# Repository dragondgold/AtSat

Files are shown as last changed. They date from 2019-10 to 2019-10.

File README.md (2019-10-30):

<h2>
</a>Desarrollo de satélite CanSat para
utilizar como plataforma educativa y
fomentar el interés en ingenierías</h2>

El objetivo principal del proyecto es el de proveer un satélite tipo CanSat completamente funcional y listo para ser utilizado, 
con una Estación Terrena para la comunicación con el mismo, a modo de plataforma educativa que permite no solo ser utilizada 
por estudiantes sin modificación alguna, sino que provee la capacidad de ser expandida para agregar o mejorar las funcionalidades 
básicas dando lugar a los estudiantes a experimentar libremente sobre una plataforma segura.

A su vez, la plataforma sera diseñada siguiendo la normativa impuesta por la European Space Agency (ESA) 
lo cual dará la posibilidad a futuro de participar de competencias de CanSat.

El proyecto está pensado para que el CanSat pueda alcanzar una altura máxima de
1000 metros aproximadamente y realice un descenso con la ayuda de un paracaídas que
limitará su velocidad para evitar la destrucción del mismo al impactar contra el suelo.
Durante esta etapa también se realizará la medición de las variables
que envía el CanSat a la Estación Terrena para luego ser interpretadas. Esto permite
analizar diversos factores respecto a la altura como los niveles de contaminación del
aire, la variabilidad de la temperatura y presión atmosférica, la toma de imágenes para
su posterior procesamiento, medición de radiación UV, composición gaseosa del aire,
etcétera.

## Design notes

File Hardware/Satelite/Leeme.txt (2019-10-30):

PCB_A -> RF + Conectores servos + Anclaje al satelite + Conexión batería + GPS + Switch y LEDs
PCB_B -> Reguladores + Protecciones + Gestión Batería
PCB_C -> Sensores + MCU Supervisor + Conector expansión limitado + micro-usb
PCB_D -> Arduino + micro-usb + Conector expansion
PCB_E -> Plaqueta preperforada + Conector expansion

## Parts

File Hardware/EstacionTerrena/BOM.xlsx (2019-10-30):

Component | Description | Part | References | Value | Footprint | Quantity Per PCB | Manufacturer Part Number
1 | Unpolarized capacitor, small symbol | C_Small | C6 C7 C8 C11 C12 C13 C14 | 100nF | C_0402_1005Metric | 7 | GCM155R71C104KA55D | 1
2 | Unpolarized capacitor, small symbol | C_Small | C2 C4 | 100nF | C_0603_1608Metric | 2 | EMK107B7104KAHT
3 | Unpolarized capacitor, small symbol | C_Small | C17 | 100pF | C_0402_1005Metric | 1 | 885012005046 | 1
4 | Unpolarized capacitor, small symbol | C_Small | C9 C10 | 15pF | C_0402_1005Metric | 2 | C0402C150J5GACTU | 1
5 | Unpolarized capacitor, small symbol | C_Small | C5 | 1uF | C_0603_1608Metric | 1 | LMK107B7105MA-T
6 | Unpolarized capacitor, small symbol | C_Small | C1 C3 | 2.2uF | C_0805_2012Metric | 2 | LMK212B7225KG-T | 1
7 | Light emitting diode | LED | D2 | Rojo | LED_0603_1608Metric | 1 | 150060RS75000 | 1
8 | Light emitting diode | LED | D1 | Verde | LED_0603_1608Metric | 1 | 150060VS75000 | 1
9 | SUBMINIATURE COAX | 5-1814832-1 | + | 5-1814832-1 | 5-1814832-1 | 1 | 5-1814832-1 | 1
10 | Generic connector, single row, 01x03, script generated (kicad-library-utils/schlib/autogen/connector/) | Conn_01x03 | J3 | Conn_01x03 | PinHeader_1x03_P2.54mm_Horizontal | 1 | 61300311121
11 | USB Micro Type B connector | USB_B_Micro | J2 | USB_B_Micro | USB_Micro-B_Molex-105017-0001 | 1 | 105017-0001
12 |  | BOM_Jumper | JP1 | BOM_Jumper | Empty_Footprint | 1 | M7581-05
13 | Inductor | L | L1 | 12nH | L_0402_1005Metric | 1 | L-07C12NJV6 | 1
14 | Resistor | R | R5 R6 | 0R | R_0402_1005Metric | 2 | RC0402JR-070RL | 1
15 | Resistor | R | R3 | 10k | R_0603_1608Metric_Pad1.05x0.95mm_HandSolder | 1 | RC0603JR-0710KL
16 | Resistor | R | R1 R2 | 220 | R_0603_1608Metric_Pad1.05x0.95mm_HandSolder | 2 | RC0603JR-13220RL
17 | Resistor | R | R4 | 56k | R_0402_1005Metric | 1 | RC0402FR-0756KL | 1
18 | Signal Conditioning 915MHz BALUN/FILTER | 0915BM15A0001E | U5 | 0915BM15A0001E | 0915BM15A0001E | 1 | 0915BM15A0001E | 1
19 | Texas Instruments CC1101RGP, RF Transceiver IC Triple Band 1.8 3.6 V 20-Pin QFN | CC1101RGP | U4 | CC1101RGP | QFN50P400X400X100-21N-D | 1 | CC1101RGP | 1
20 | USB-to-SPI Protocol Converter with GPIO (Master Mode) | MCP2210 | U3 | MCP2210 | SSOP-20_5.3x7.2mm_P0.65mm | 1 | MCP2210-I/SS | 1
21 | Micrel MIC5323-3.3YD5 TR, LDO Voltage Regulator, 300mA, 3.3 V 2%, 2.65 5.5 Vin, 5-Pin TSOT-23 | MIC5323-3.3YD5_TR | U2 | MIC5323-3.3YD5_TR | SOT95P280X100-5N | 1 | MIC5323-3.3YD5 TR | 1
22 | Dual-Channel High-Speed ESD Protection | TPD2E2U06 | U1 | TPD2E2U06 | SOT-553 | 1 | TPD2E2U06DRLR | 1
23 | Three pin crystal, GND on pin 2 | Crystal_GND2 | Y1 | 12MHz | Resonator_SMD_muRata_CSTxExxV-3Pin_3.0x1.1mm | 1 | CSTNE12M0GH5L000R0 | 1
24 | Four pin crystal, GND on pins 2 and 4 | Crystal_GND24 | Y2 | 26 MHz | Crystal_SMD_2520-4Pin_2.5x2.0mm | 1 | FA-20H 26.0000MF12V-W | 1

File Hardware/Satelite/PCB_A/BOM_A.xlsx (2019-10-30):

Component | Description | Part | References | Value | Footprint | Quantity Per PCB | Manufacturer Part Number
1 | Unpolarized capacitor, small symbol | C_Small | C2 C4 C5 C6 C9 C10 C11 C12 | 100nF | C_0402_1005Metric | 8 | GCM155R71C104KA55D
2 | Unpolarized capacitor, small symbol | C_Small | C15 | 100pF | C_0402_1005Metric | 1 | 885012005046
3 | Unpolarized capacitor, small symbol | C_Small | C7 C8 | 15pF | C_0402_1005Metric | 2 | C0402C150J5GACTU
4 | Unpolarized capacitor, small symbol | C_Small | C1 C3 | 1uF | C_0603_1608Metric_Pad1.05x0.95mm_HandSolder | 2 | LMK107B7105MA-T
5 | Light emitting diode | LED | D1 | Rojo | LED_0603_1608Metric_Pad1.05x0.95mm_HandSolder | 1 | 150060RS75000
6 | Light emitting diode | LED | D2 | Verde | LED_0603_1608Metric_Pad1.05x0.95mm_HandSolder | 1 | 150060VS75000
7 | Resettable fuse, polymeric positive temperature coefficient | Polyfuse | F1 | Polyfuse | Fuse_1812_4532Metric_Pad1.30x3.40mm_HandSolder | 1 | 0ZCG0150FF2C
8 | RF Connectors / Coaxial Connectors U.FL Straight Surface Mount Jack | CONUFL001-SMD | J2 | CONUFL001-SMD | CONUFL001-SMD | 1 | CONUFL001-SMD
9 |  | Conector_PCB_A-B | J4 | Conector_PCB_A-B | Conector_PCB_A-B | 3 | 22-28-5034
10 |  |  | J4 | Conector_PCB_A-B | Conector_PCB_A-B | 2 | 22-28-4041
11 | Generic connector, single row, 01x03, script generated (kicad-library-utils/schlib/autogen/connector/) | Conn_01x03 | J3 | Servo Globo | PinHeader_1x03_P2.54mm_Vertical | 1 | 61300311121
12 | Generic connector, single row, 01x03, script generated (kicad-library-utils/schlib/autogen/connector/) | Conn_01x03 | J5 | Servo ParacaÃdas | PinHeader_1x03_P2.54mm_Vertical | 1 | 61300311121
13 | Inductor | L | L1 | 12nH | L_0402_1005Metric | 1 | L-07C12NJV6
14 |  | Spacer | M1 M2 M3 | Spacer | Empty_Footprint | 3 | R30-3011002
15 | 0.8A Ic, 45V Vce, NPN Transistor, SOT-23 | BC817 | Q2 | BC817 | SOT-23 | 1 | BC817-16LT1G
16 | MOSFET Small-signal MOSFET Vdss= -12V, ID= -6A | SSM3J338R,LF | Q1 | SSM3J338R,LF | SSM3J332RLFT | 1 | SSM3J338R,LF
17 | Resistor | R | R9 R10 | 0R | R_0402_1005Metric | 2 | RC0402JR-070RL
18 | Resistor | R | R3 R4 R5 R6 R7 | 10k | R_0603_1608Metric_Pad1.05x0.95mm_HandSolder | 5 | RC0603JR-0710KL
19 | Resistor | R | R1 R2 | 1k | R_0603_1608Metric_Pad1.05x0.95mm_HandSolder | 2 | RC0603JR-071KL
20 | Resistor | R | R8 | 56k | R_0402_1005Metric | 1 | RC0402FR-0756KL
21 | Slide Switches SPDT RA SLIDE PC MNT | 500SSP1S1M6QEA | S1 | 500SSP1S1M6QEA | 500SSP1S1M6QEA | 1 | 500SSP1S1M6QEA
22 | Signal Conditioning 915MHz BALUN/FILTER | 0915BM15A0001E | U3 | 0915BM15A0001E | 0915BM15A0001E | 1 | 0915BM15A0001E
23 | GPS Modules SiRFStarIV GPS receiver SMT ROM mod | A2235-H | U1 | A2235-H | A2235-H | 1 | A2235-H
24 | Texas Instruments CC1101RGP, RF Transceiver IC Triple Band 1.8 3.6 V 20-Pin QFN | CC1101RGP | U2 | CC1101RGP | QFN50P400X400X100-21N-D | 1 | CC1101RGP
25 | Four pin crystal, GND on pins 2 and 4 | Crystal_GND24 | Y1 | 26 MHz | Crystal_SMD_2520-4Pin_2.5x2.0mm | 1 | FA-20H 26.0000MF12V-W

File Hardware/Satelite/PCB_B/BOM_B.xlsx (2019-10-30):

Component | Description | Part | References | Value | Footprint | Quantity Per PCB | Manufacturer Part Number
1 | Unpolarized capacitor, small symbol | C_Small | C27 | 0.47uF | C_0603_1608Metric_Pad1.05x0.95mm_HandSolder | 1 | 885012206024
2 | Unpolarized capacitor, small symbol | C_Small | C4 C7 C11 C13 C15 C21 C22 | 100nF | C_0603_1608Metric_Pad1.05x0.95mm_HandSolder | 7 | EMK107B7104KAHT
3 | Unpolarized capacitor, small symbol | C_Small | C19 | 10n | C_0603_1608Metric_Pad1.05x0.95mm_HandSolder | 1 | 06033C103K4T2A
4 | Unpolarized capacitor, small symbol | C_Small | C1 C2 C6 C10 C14 C18 | 10uF | C_0805_2012Metric_Pad1.15x1.40mm_HandSolder | 6 | C2012X7R1A106M125AC
5 | Unpolarized capacitor, small symbol | C_Small | C8 C9 C12 C16 C17 C20 C23 C24 C25 C26 | 1uF | C_0603_1608Metric_Pad1.05x0.95mm_HandSolder | 10 | LMK107B7105MA-T
6 | Unpolarized capacitor, small symbol | C_Small | C3 C5 | 2.2uF | C_0805_2012Metric_Pad1.15x1.40mm_HandSolder | 2 | LMK212B7225KG-T
7 | Switching Voltage Regulators Step-up DC/DC Reg 1 MHz, 1.6A, 5Vout | MCP1642B-50I_MS | IC1 IC2 | MCP1642B-50I_MS | SOP65P490X110-8N | 2 | MCP1642B-50I/MS
8 |  | Conector_PCB_A-B | J2 | Conector_PCB_A-B | Conector_PCB_A-B | 3 | CES-103-01-T-S
9 |  | Conector_PCB_A-B | J2 | Conector_PCB_A-B | Conector_PCB_A-B | 2 | CES-104-01-T-S
10 |  | Conector_PCB_B-C | J1 | Conector_PCB_B-C | Conector_PCB_B-C_Lado_B | 2 | 10132798-022100LF
11 | Inductor with iron core | L_Core_Iron | L2 | 1uH | L_0805_2012Metric_Pad1.15x1.40mm_HandSolder | 1 | LQM21PN1R0MC0D
12 | Inductor with iron core | L_Core_Iron | L1 L3 | 4.7uH | SRN3010TA-4R7M | 2 | SRN3010TA-4R7M
13 |  | Spacer | M1 M2 M3 | Spacer | Empty_Footprint | 3 | R30-3011202
14 | Resistor | R | R16 R22 | 100k | R_0603_1608Metric_Pad1.05x0.95mm_HandSolder | 2 | RC0603JR-07100KL
15 | Resistor | R | R20 R21 | 10k | C_0603_1608Metric_Pad1.05x0.95mm_HandSolder | 2 | RC0603JR-0710KL
16 | Resistor | R | R17 | 10m | R_2512_6332Metric_Pad1.52x3.35mm_HandSolder | 1 | KRL3264-C-R010-F-T1
17 | Resistor | R | R2 | 120m | R_1206_3216Metric_Pad1.42x1.75mm_HandSolder | 1 | KRL1632E-M-R120-F-T5
18 | Resistor | R | R5 | 150k | R_0603_1608Metric_Pad1.05x0.95mm_HandSolder | 1 | RC0603FR-07150KL
19 | Resistor | R | R14 | 1k8 | R_0603_1608Metric_Pad1.05x0.95mm_HandSolder | 1 | RC0603FR-071K8L
20 | Resistor | R | R7 | 200m | R_1206_3216Metric_Pad1.42x1.75mm_HandSolder | 1 | KRL1632E-C-R200-F-T5
21 | Resistor | R | R9 | 22k | R_0603_1608Metric_Pad1.05x0.95mm_HandSolder | 1 | RC0603FR-1322KL
22 | Resistor | R | R4 R15 | 2k | R_0603_1608Metric_Pad1.05x0.95mm_HandSolder | 2 | RC0603FR-102KL
23 | Resistor | R | R10 | 39k | R_0603_1608Metric_Pad1.05x0.95mm_HandSolder | 1 | RC0603FR-1339KL
24 | Resistor | R | R1 R3 R6 R8 R11 R13 | 51R | R_0603_1608Metric_Pad1.05x0.95mm_HandSolder | 6 | AC0603FR-0751RL
25 | Resistor | R | R12 | 51m | R_1206_3216Metric_Pad1.42x1.75mm_HandSolder | 1 | KRL1632E-C-R051-F-T1
26 | 3MHz switching bucK regulator, 600mA 3.3V output voltage, | ADP2108AUJ-3.3 | U2 | ADP2108AUJ-3.3 | TSOT-23-5 | 1 | ADP2108AUJZ-3.3-R7
27 | Texas Instruments BQ24091DGQT, Battery Charge Controller, 1000mA, 10-Pin MSOP | BQ24091DGQT | U8 | BQ24091DGQT | SOP50P490X110-11N | 1 | BQ24091DGQT
28 | System Side Li Ion/Polymer Fuel Gauge, 4.2V, PDSON-12 | BQ27441DRZR-G1A | U9 | BQ27441DRZR-G1A | Texas_S-PDSO-N12 | 1 | BQ27441DRZR-G1A
29 | Current Shunt Monitor âˆ’16 V to +80 V Common-Mode Range, 50V/V, SOT-23-5 | INA194 | U3 U5 U7 | INA194 | SOT-23-5 | 3 | INA194AIDBVR
30 | 1MHz, Low-Power Op Amp, SOT-23-5 | MCP6001-OT | U4 U6 | MCP6001-OT | SOT-23-5 | 2 | MCP6001T-I/OT
31 | Micrel MIC5323-3.3YD5 TR, LDO Voltage Regulator, 300mA, 3.3 V 2%, 2.65 5.5 Vin, 5-Pin TSOT-23 | MIC5323-3.3YD5_TR | U1 | MIC5323-3.3YD5_TR | SOT95P280X100-5N | 1 | MIC5323-3.3YD5 TR

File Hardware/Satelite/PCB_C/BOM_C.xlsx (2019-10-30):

Component | Description | Part | References | Value | Footprint | Quantity Per PCB | Manufacturer Part Number
1 | Unpolarized capacitor, small symbol | C_Small | C2 C5 C9 C11 C19 C21 C22 C24 C25 | 100nF | C_0402_1005Metric | 9 | GCM155R71C104KA55D
2 | Unpolarized capacitor, small symbol | C_Small | C1 C13 C16 C23 | 1uF | C_0402_1005Metric | 4 | GRM155R70J105KA12J
3 | Unpolarized capacitor, small symbol | C_Small | C3 C4 | 4.3pF | C_0402_1005Metric | 2 | GRM1555C1H4R3WA01D
4 | Small versatile 9-axis sensor module | BMX055 | IC5 | BMX055 | LGA_PACKAGE_20_PINS | 1 | BMX055
5 | SPST USB 2.0 High-Speed Switch With Battery Charging Detection | BQ24392RSER | IC3 | BQ24392RSER | RSE(R-PUQFN-N10) | 1 | BQ24392RSER
6 | NOR Flash 8Mb QSPI, 8-pin USON 2x3mm, RoHS, T&R | IS25LP080D-JULE-TR | IC2 | IS25LP080D-JULE-TR | SON50P200X300X60-8N | 1 | IS25LP080D-JULE-TR
7 | Voltage References Precision Buffered Voltage Reference | MCP1501T-33E_CHY | IC1 | MCP1501T-33E_CHY | SOT95P270X145-6N | 1 | MCP1501T-33E/CHY
8 | Sensor Pressure 2bar Barometric SMD MS563702BA03-50, Barometric Pressure Sensor, 1200mbar 0 ??? 3.6 V Output, 4-Pin QFN | MS563702BA03-50 | IC4 | MS563702BA03-50 | MS5637_1 | 1 | MS563702BA03-50
9 |  | Conector_Expansion_CanSat | J4 | Conector_Expansion_CanSat | Conector_Expansion_CanSat | 4 | SSQ-106-03-T-S
10 |  | Conector_PCB_B-C | J3 | Conector_PCB_B-C | Conector_PCB_B-C_Lado_C | 2 | 10132797-025100LF
11 | Generic connector, single row, 01x06, script generated (kicad-library-utils/schlib/autogen/connector/) | Conn_01x06 | J1 | Conn_01x06 | PinHeader_1x06_P2.54mm_Vertical | 1 | 68000-406HLF
12 | Generic connector, double row, 02x03, counter clockwise pin numbering scheme (similar to DIP packge numbering), script generated (kicad-library-utils/schlib/autogen/connector/) | Conn_02x03_Counter_Clockwise | J6 | Conn_02x03_Counter_Clockwise | PinHeader_2x03_P1.27mm_Vertical_SMD | 1 | TSM-103-04-T-DV
13 | USB Micro Type B connector | USB_B_Micro | J5 | USB_B_Micro | USB_Micro-B_Molex-105017-0001 | 1 | 105017-0001
14 |  | BOM_Jumper | JP1 | BOM_Jumper | Empty_Footprint | 1 | M7581-05
15 |  | Spacer | M1 M2 M3 | Spacer | Empty_Footprint | 3 | R30-3011002
16 | Resistor | R | R5 R6 R7 | 100k | R_0603_1608Metric_Pad1.05x0.95mm_HandSolder | 3 | RC0603JR-07100KL
17 | Resistor | R | R1 R2 R3 R4 R5 | 10k | R_0603_1608Metric_Pad1.05x0.95mm_HandSolder | 5 | RC0603JR-0710KL
18 | NXP - NTB0104BQ,115 - TRANSCEIVER, BIDIR TRANSLATOR, DHVQFN14 | NTB0104BQ,115 | U1 U4 | NTB0104BQ,115 | NTB0104BQ115 | 2 | NTB0104BQ,115
19 |  | ESP32-WROOM-32-RF_Module | U3 | ESP32-WROOM-32 | ESP32-WROOM-32 | 1 | ESP32-WROOM-32
20 | Si7006 Digital RH temp sensor w filter Silicon Labs Si7006-A20-IM1 Temperature & Humidity Sensor, -40 +125 C, 6-Pin DFN | Si7006-A20-IM1 | U6 | Si7006-A20-IM1 | SON100P300X300X80-7N | 1 | Si7006-A20-IM1
21 | PIC16LF18325, 8192W FLASH, 1024B SRAM, SOIC14 | PIC16LF18325-ISL | U7 | PIC16LF18325-ISL | SOIC-14_3.9x8.7mm_P1.27mm | 1 | PIC16LF18325-I/SL
22 | Level-Translating I2C Bus Buffer/Repeater | TCA9802DGKR | U2 | TCA9802DGKR | SOP65P490X110-8N | 1 | TCA9802DGKR
23 | Two pin crystal | Crystal | Y2 | Crystal | Crystal_HC49-4H_Vertical | 1 | LFXTAL029665
24 | IQD FREQUENCY PRODUCTS - LFXTAL016178 - CRYSTAL, 32.768KHZ, 6PF, SMD | LFXTAL016178 | Y1 | LFXTAL016178 | LFXTAL016178_1 | 1 | LFXTAL016178

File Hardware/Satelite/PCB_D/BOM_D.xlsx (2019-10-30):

Component | Description | Part | References | Value | Footprint | Quantity Per PCB | Manufacturer Part Number
1 | Unpolarized capacitor, small symbol | C_Small | C1 C3 C4 | 100n | C_0603_1608Metric_Pad1.05x0.95mm_HandSolder | 3 | EMK107B7104KAHT
2 | Unpolarized capacitor, small symbol | C_Small | C2 | 1uF | C_0603_1608Metric_Pad1.05x0.95mm_HandSolder | 1 | LMK107B7105MA-T
3 | Unpolarized capacitor, small symbol | C_Small | C5 | 4.7uF | C_0805_2012Metric_Pad1.15x1.40mm_HandSolder | 1 | GRM21BR71A475KE51K
4 | 1000V 1A General Purpose Rectifier Diode, DO-41 | 1N4007 | D4 | 1N4007 | D_SMA | 1 | S1K-13-F
5 | 100V 0.15A standard switching diode, MiniMELF | LL4148 | D5 D6 | LL4148 | D_MiniMELF | 2 | LL4148-GS08
6 | Light emitting diode | LED | D3 | Rojo | LED_0603_1608Metric | 1 | 150060RS75000
7 | Light emitting diode | LED | D1 D2 | Verde | LED_0603_1608Metric | 2 | 150060VS75000
8 |  | Conector_Expansion_CanSat | J2 | Conector_Expansion_CanSat | Conector_Expansion_CanSat | 4 | SSQ-106-03-T-S
9 | Generic connector, single row, 01x03, script generated (kicad-library-utils/schlib/autogen/connector/) | Conn_01x03 | J1 J5 | Conn_01x03 | PinHeader_1x03_P2.54mm_Vertical | 2 | 61300311121
10 | Generic connector, double row, 02x03, odd/even pin numbering scheme (row 1 odd numbers, row 2 even numbers), script generated (kicad-library-utils/schlib/autogen/connector/) | Conn_02x03_Odd_Even | J3 | Conn_02x03_Odd_Even | PinHeader_2x03_P2.54mm_Vertical | 1 | TSM-103-03-T-DV
11 | USB Micro Type B connector | USB_B_Micro | J4 | USB_B_Micro | USB_Micro-B_Molex-105017-0001 | 1 | 105017-0001
12 |  | BOM_Jumper | JP1 | BOM_Jumper | Empty_Footprint | 1 | M7581-05
13 |  | Spacer | M1 M2 M3 | Spacer | Empty_Footprint | 3 | R30-3011002
14 | Resistor | R | R1 | 100K | R_0603_1608Metric_Pad1.05x0.95mm_HandSolder | 1 | RC0603JR-07100KL
15 | Resistor | R | R2 R3 | 10k | R_0603_1608Metric_Pad1.05x0.95mm_HandSolder | 2 | RC0603JR-0710KL
16 | Resistor | R | R4 R5 R6 | 220 | R_0603_1608Metric_Pad1.05x0.95mm_HandSolder | 3 | RC0603JR-13220RL
17 | Push button switch, generic, two pins | SW_Push | SW1 | Reset Switch | SW_PUSH_6mm | 1 | FSM18JH
18 | 20MHz, 32kB Flash, 2kB SRAM, 1kB EEPROM, TQFP-32 | ATmega328P-AU | U1 | ATmega328P-AU | TQFP-32_7x7mm_P0.8mm | 1 | ATMEGA328P-AU
19 | Resonators 16.0000MHz 15pF SMD CHP Resntr | CSTNE16M0V530000R0 | U2 | CSTNE16M0V530000R0 | CSTNE16M0V530000R0 | 1 | CSTNE16M0V530000R0
20 | Full Speed USB to Full Handshake UART, SSOP-20 | FT231XS | U3 | FT231XS | SSOP-20_3.9x8.7mm_P0.635mm | 1 | FT231XS-U
21 | Dual-Channel High-Speed ESD Protection | TPD2E2U06 | U4 | TPD2E2U06 | SOT-553 | 1 | TPD2E2U06DRLR

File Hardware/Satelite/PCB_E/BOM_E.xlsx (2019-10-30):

Component | Description | Part | References | Value | Footprint | Quantity Per PCB | Manufacturer Part Number
1 |  | Conector_Expansion_CanSat | J12 | Conector_Expansion_CanSat | Conector_Expansion_CanSat | 4 | SSQ-106-03-T-S
4 |  | Spacer | M1 M2 M3 | Spacer | Empty_Footprint | 3 | R30-3011002

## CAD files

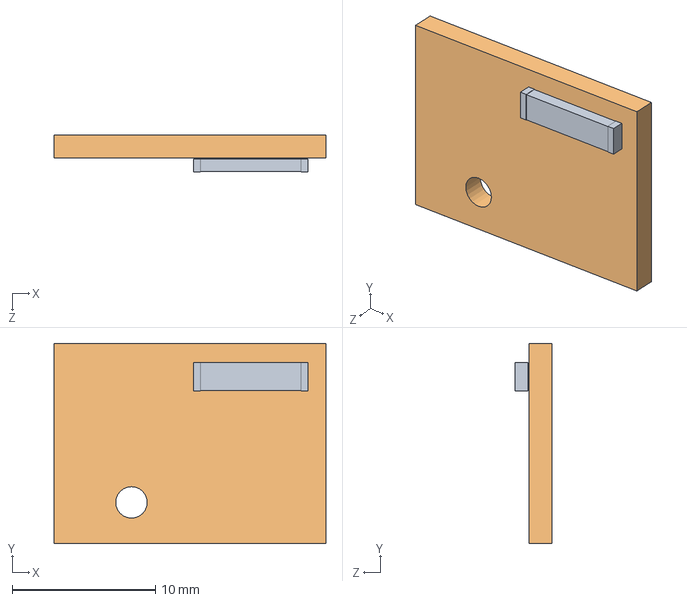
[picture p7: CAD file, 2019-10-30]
Estructura mecanica/Satelite/Antena.SLDASM
19.0 x 14.0 x 2.55 mm

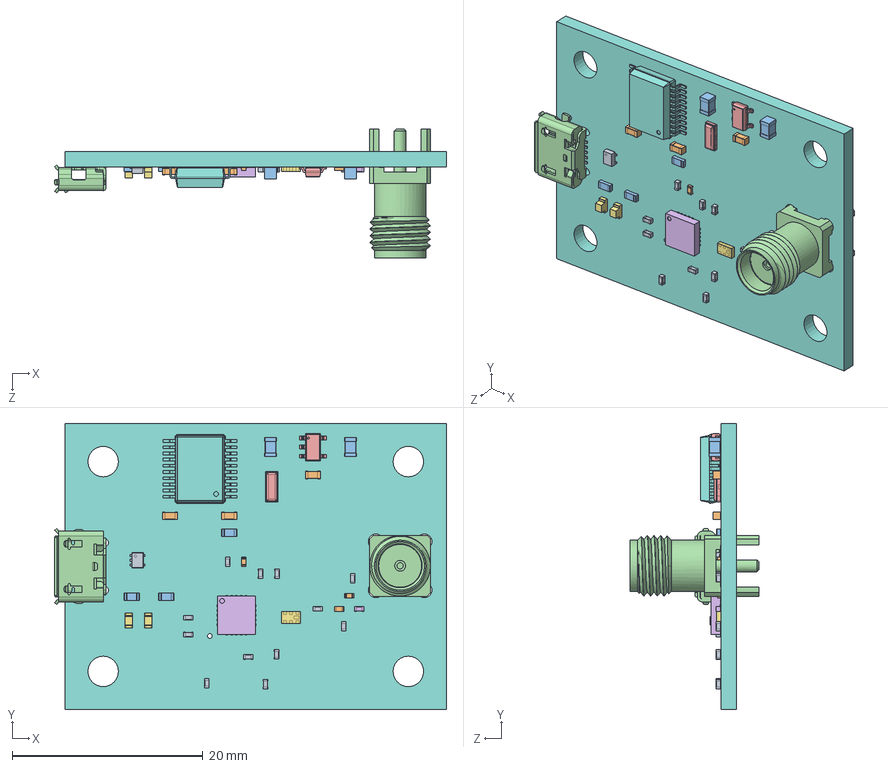
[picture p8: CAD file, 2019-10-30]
Estructura mecanica/Estacion terrena/asmPCBET/EstacionTerrena.SLDASM
41.1 x 30.0 x 13.5 mm

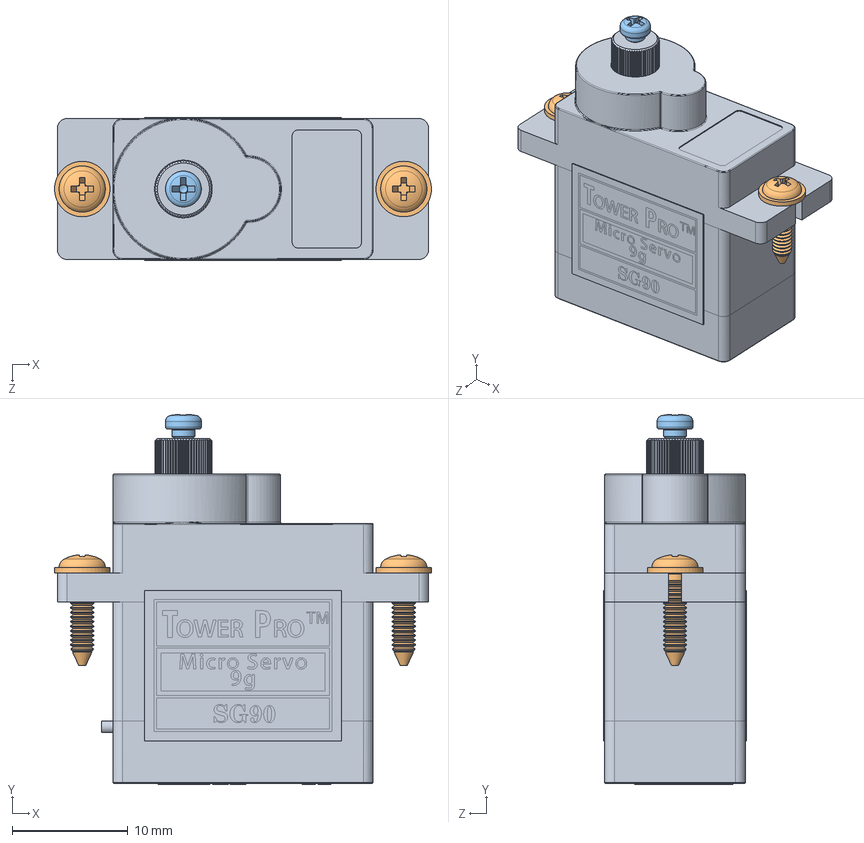
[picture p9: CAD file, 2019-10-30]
Estructura mecanica/Satelite/micro-servo/SG90 - Micro Servo 9g - Tower Pro.SLDASM
32.6 x 32.0 x 12.4 mm
SG90 - Micro Servo 9g - Tower Pro.1
SG90 - Micro Servo 9g - Tower Pro.5 x 2
SG90 - Micro Servo 9g - Tower Pro.6

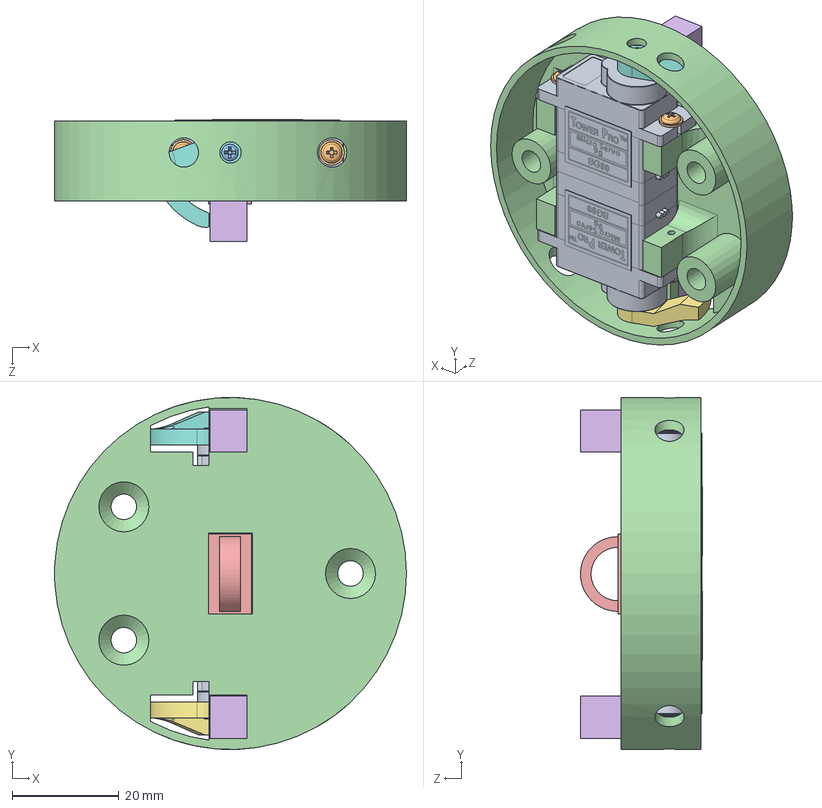
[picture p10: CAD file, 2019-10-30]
Estructura mecanica/Satelite/actuadoresSat.SLDASM
66.0 x 66.0 x 22.9 mm
SG90 - Micro Servo 9g - Tower Pro.1 x 2
SG90 - Micro Servo 9g - Tower Pro.5 x 4
SG90 - Micro Servo 9g - Tower Pro.6 x 2
pisoParacaida
enganche de paracaida y globo
topesServos x 2
nuevo-brazo-servo
nuevo-brazo-servo-espejado

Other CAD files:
Estructura mecanica/Estacion terrena/asmPCBET/C_0805_2012Metric.sldasm
Estructura mecanica/Satelite/0915AT43A0026E.sldasm
Estructura mecanica/Estacion terrena/asmPCBET/CSTNE12M0GH5L000R0.sldasm
Estructura mecanica/Estacion terrena/asmPCBET/USB_Micro-B_Molex_47346-0001.sldasm
Estructura mecanica/Estacion terrena/asmPCBET/R_0402_1005Metric.sldasm
Estructura mecanica/Estacion terrena/asmPCBET/MIC5323-3.3YD5_TR.sldasm
Estructura mecanica/Estacion terrena/asmPCBET/R_0603_1608Metric.sldasm
Estructura mecanica/Estacion terrena/asmPCBET/SOT-553.sldasm
Estructura mecanica/Estacion terrena/asmPCBET/CC1101RGP.sldasm
Estructura mecanica/Estacion terrena/asmPCBET/5-1814832-1.sldasm
Estructura mecanica/Estacion terrena/asmPCBET/C_0603_1608Metric.sldasm
Estructura mecanica/Estacion terrena/asmPCBET/SSOP-20_5.3x7.2mm_P0.65mm.sldasm
Estructura mecanica/Estacion terrena/asmPCBET/L_0402_1005Metric.sldasm
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

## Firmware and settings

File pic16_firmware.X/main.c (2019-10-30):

/**
 * This program samples all 5 channels to measure voltages and currents in
 *  the AXTEC CanSat platform. As we are very CPU constrained we have to do
 *  some tradeoffs in order to make this work, maybe a real ADC chip will do
 *  better in the future.
 * 
 * The firmware samples 13 times all the channels. Every channel and conversion
 *  takes about 29us (plus code and interrupt overhead, the XC8 compiler and
 *  PIC16 architecture aren't the most efficient) so the 5 channels are sampled
 *  every 29*5=145us. After sampling this 13 times, 145*13=1885us were spent
 *  sampling and the accumulated results are stored in the results[]. The ESP32
 *  has then to take the accumulated values and divide them by 13, it's fast for
 *  him, very slow for us that's we don't do it here.
 * 
 * After taking the 13 samples the sampling is stopped and the SDA and SCL lines
 *  are taken from high to low to indicate the ESP32 that data is ready (this is
 *  possible because we are the only device in the I2C bus), also the TMR0 is
 *  started to fire an interrupt after 4ms. This is all the time the ESP32 has
 *  to read the data from the PIC16 before it starts a new sampling process
 *  disabling the I2C again.
 * 
 * We have to disable the I2C because the sampling takes 100% of the CPU time so
 *  we can't process the I2C events at the same time.
 */

#include "mcc_generated_files/mcc.h"
#include "i2c_slave_manager.h"
#include "main.h"

// The last index is NOT used, it's to avoid an additional check in the ISR
static adc_channel_t channels[] = {V3V3,V5V,I3V3,I5V,IBAT};
static int8_t channel_index = 0;
static uint8_t sample_counter = 0;

// They results are in the same order as in channels_all[] array
uint16_t results[] = {0, 0, 0, 0, 0};
static __bit data_ready = 0;

// The timer interrupt is fired 4ms after being started
void tmr0_isr(void) 
{
    // Stop the timer
    T0CON0bits.T0EN = 0;
    // Disable I2C
    SSP1CON1bits.SSPEN = 0;
    PIE1bits.SSP1IE = 0;
    SCL1_SetDigitalInput();
    SDA1_SetDigitalInput();
    
    // Clear the results
    results[0] = 0;
    results[1] = 0;
    results[2] = 0;
    results[3] = 0;
    results[4] = 0;
    
    // Restart the ADC sampling process. Select the channel.
    ADCON0bits.CHS = channels[channel_index];
    
    // Load the time to wait for 6 us for the sampling time.
    PIR1bits.TMR2IF = 0;
    PR2 = 0x2F;
    T2CONbits.TMR2ON = 1;
    while(!PIR1bits.TMR2IF);
    
    // Start the conversion
    ADCON0bits.ADGO = 1;
}

void adc_isr(void)
{
    // Clear the ADC interrupt flag
    PIR1bits.ADIF = 0;

    // All the channels haven been sampled
    if(channel_index == (sizeof(results)/sizeof(uint16_t))-1)
    {
        /**
         * Yes, this code duplication is ugly, but is much faster than additional
         *  checks
         */
        // Keep going!
        channel_index = 0;
        
        // Select the next channel. This takes 14 instructions!!! The free XC8 compiler
        //  is as bad as me writing assembler code.
        ADCON0bits.CHS = channels[0];

        // Load the time to wait for 6 us for the sampling time. We use the timer
        //  so we can execute other operation while waiting the sampling time.
        PIR1bits.TMR2IF = 0;
        PR2 = 0x2F;
        T2CONbits.TMR2ON = 1;

        // Store the result of the last channel sampled
        results[(sizeof(results)/sizeof(uint16_t))-1] += ((ADRESH << 8) + ADRESL);
        
        if(++sample_counter == SAMPLES_PER_BATCH)
        {
            // Store the result
            CLRWDT();
            sample_counter = 0;
            channel_index = 0;
            
            // Start the timer to start the sampling process later
            TMR0H = 0x3E;
            TMR0L = 0x00;
            T0CON0bits.T0EN = 1;
            
            // Mark as data ready
            data_ready = 1;
            return;
        }
        
        // Wait for timer to fire
        while(!PIR1bits.TMR2IF);
        
        // Start sampling the new channel
        ADCON0bits.ADGO = 1;
        return;
    }
    
    // Select the next channel. This takes 14 instructions!!! The free XC8 compiler
    //  is as bad as me writing assembler code.
    ADCON0bits.CHS = channels[channel_index+1];
    
    // Load the time to wait for 6 us for the sampling time. We use the timer
    //  so we can execute other operation while waiting the sampling time.
    PIR1bits.TMR2IF = 0;
    PR2 = 0x2F;
    T2CONbits.TMR2ON = 1;
    
    // Store the result, add all the result. The reader must then do an average.
    // We don't do that here because we don't have TIME. This CPU is slow for
    //  the job.
    results[channel_index++] += ((ADRESH << 8) + ADRESL);
    
    // Wait for timer to fire
    while(!PIR1bits.TMR2IF);
    
    // Start sampling the new channel
    ADCON0bits.ADGO = 1;
}

void main(void)
{
    // Initialize the device
    SYSTEM_Initialize();
    i2c_slave_manager_init();
    
    CLRWDT();

    // Enable the Global Interrupts
    INTERRUPT_GlobalInterruptEnable();
    // Enable the Peripheral Interrupts
    INTERRUPT_PeripheralInterruptEnable();
    
    // Stop the timer and set the interrupt handler
    TMR0_StopTimer();
    TMR0_SetInterruptHandler(tmr0_isr);
    TMR2_StopTimer();
    
    // Fire the timer, after the timer elapses the ADC will start working 
    TMR0H = 0x3E;
    TMR0L = 0x00;
    TMR0_StartTimer();
    
    // Start with I2C module off
    i2c1_driver_close();
    PIE1bits.SSP1IE = 0;
    SCL1_SetDigitalInput();
    SDA1_SetDigitalInput();
    
    while(1)
    {
        // Data ready, toggle the SDA and SCL lines from high to low
        //  as an indication that the ESP32 can now read from I2C
        if(data_ready)
        {
            // Set SCL and SDA low for 10 us
            SCL1_SetLow();
            SDA1_SetLow();
            SCL1_SetDigitalOutput();
            SDA1_SetDigitalOutput();
            __delay_us(50);
            SCL1_SetDigitalInput();
            SDA1_SetDigitalInput();
            
            // Enable I2C again and wait!
            data_ready = 0;
            i2c_slave_manager_init();
        }   
    }
}

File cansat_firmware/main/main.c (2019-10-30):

/*
 Firmware para el satélite CanSat desarrollado por AXTEC y distribuido
  bajo la licencia GNU GPL V3.0.

  Autor: Andrés Fernando Torti
  Fecha: 21/01/2019
*/
#include <stdio.h>
#include "freertos/FreeRTOS.h"
#include "freertos/task.h"
#include "freertos/timers.h"
#include "esp_system.h"
#include "esp_spi_flash.h"
#include "driver/gpio.h"
#include "esp_err.h"
#include "config/cansat.h"

#include "aux_ps/aux_ps.h"
#include "i2c_manager/i2c_manager.h"
#include "spi_manager/spi_manager.h"
#include "sensor_manager/sensor_manager.h"
#include "battery_manager/battery_manager.h"
#include "servo_manager/servo_manager.h"
#include "led_manager/led_manager.h"
#include "com_manager/com_manager.h"
#include "power_monitor/power_monitor.h"
#include "sup_cmd_manager/sup_cmd_manager.h"
#include "console_manager/console_manager.h"

#ifdef DEBUG
    #define LOG_LOCAL_LEVEL ESP_LOG_DEBUG
#endif
#include "esp_log.h"

static const char* TAG = "main";

#ifdef DEBUG
/**
 * @brief Print information about the system. For this to work configUSE_TRACE_FACILITY must be enabled
 *  using 'make menuconfig' then selecting 'Component config->FreeRTOS->Enable FreeRTOS trace facility'
 */
void vGetRunTimeStats(TimerHandle_t xTimer)
{
    ESP_LOGD(TAG, "Getting runtime data");

    TaskStatus_t *pxTaskStatusArray;
    volatile UBaseType_t uxArraySize, x;

    // Take a snapshot of the number of tasks in case it changes while this
    // function is executing.
    uxArraySize = uxTaskGetNumberOfTasks();
    ESP_LOGD(TAG, "%d tasks running", uxArraySize);

    // Allocate a TaskStatus_t structure for each task.  An array could be
    // allocated statically at compile time.
    pxTaskStatusArray = pvPortMalloc( uxArraySize * sizeof( TaskStatus_t ) );

    if(pxTaskStatusArray != NULL)
    {
        // Generate raw status information about each task.
        uxArraySize = uxTaskGetSystemState(pxTaskStatusArray, uxArraySize, NULL);

        // For each populated position in the pxTaskStatusArray array,
        // format the raw data as human readable ASCII data
        for( x = 0; x < uxArraySize; x++ )
        {
            ESP_LOGD(TAG, "------ Task \"%s\"", pxTaskStatusArray[x].pcTaskName);
            ESP_LOGD(TAG, "Free stack: %d bytes", pxTaskStatusArray[x].usStackHighWaterMark);
        }

        // The array is no longer needed, free the memory it consumes.
        vPortFree(pxTaskStatusArray);
    }
    else
    {
        ESP_LOGD(TAG, "------ pxTaskStatusArray is NULL");
    }

    ESP_LOGD(TAG, "------ Finished vGetRunTimeStats()");
}
#endif

void app_main()
{
    ESP_LOGI(TAG, "System boot!");

    // Get chip information and output it
    esp_chip_info_t chip_info;
    esp_chip_info(&chip_info);
    ESP_LOGI(TAG, "ESP32 with %d CPU cores. Revision %d.",
            chip_info.cores,
            chip_info.revision);

    // Flash information
    ESP_LOGI(TAG, "%dMB %s flash\n", spi_flash_get_chip_size() / (1024 * 1024),
            (chip_info.features & CHIP_FEATURE_EMB_FLASH) ? "embedded" : "external");
    fflush(stdout);

    // Init every system in the satellite
    esp_err_t err = ESP_OK;
    ESP_LOGI(TAG, "Initializing systems");

    // Install gpio isr service
    gpio_install_isr_service(ESP_INTR_FLAG_IRAM);

    err += led_manager_init();
    led_manager_fast_blink(true);

    err += aux_ps_init();
    err += i2c_manager_init();
    err += spi_manager_init();
    err += sensor_manager_init();
    err += battery_manager_init();
    err += servo_manager_init();
    err += com_manager_init();
    err += power_monitor_init();
    err += sup_cmd_manager_init();
    //err += console_manager_init();

    ESP_LOGI(TAG, "RAM left: %d bytes", esp_get_free_heap_size());

    if(err == ESP_OK)
    {
        ESP_LOGI(TAG, "Systems ready!");
        led_manager_on();

        // Enable PSU now that the protections are enabled
        aux_ps_enable();
    }
    else
    {
        ESP_LOGE(TAG, "------ System init failed! ------");
        led_manager_fast_blink(false);
    }

// When debug is defined, print the system status after 3 seconds running
#ifdef DEBUG
    if(xTimerStart((int)xTimerCreate("stats_tmr", pdMS_TO_TICKS(3000), pdFALSE, (void *)0, vGetRunTimeStats), 500 / portTICK_PERIOD_MS) == pdFAIL)
    {
        ESP_LOGE(TAG, "Error starting timer");
    }
#endif
}

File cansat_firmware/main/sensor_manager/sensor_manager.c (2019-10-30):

#include "sensor_manager.h"

#include "config/cansat.h"
#include "esp_system.h"
#include "freertos/FreeRTOS.h"
#include "esp_log.h"
#include "libs/sensor_fusion/sensor_fusion.h"
#include "libs/minmea/minmea.h"
#include "esp_timer.h"
#include "servo_manager/servo_manager.h"

#include "gps_manager/gps_manager.h"
#include "imu_manager/imu_manager.h"
#include "pressure_manager/pressure_manager.h"
#include "humidity_manager/humidity_manager.h"

#include <string.h>

static const char* TAG = "sensor";

static sensors_data_t sensors_data;
static float last_altitude = 0;
static bool got_first_altitude = false;
static float altitude_change = 0;
static sensors_data_t sensors_samples[SENSOR_MANAGER_MAX_SAMPLES_TO_STORE] = { 0 };

// Sensor fusion
static SensorFusionGlobals sfg;                 // Sensor fusion instance
static struct PhysicalSensor sensors[3];        // Storage for the sensors used
static registerDeviceInfo_t i2cBusInfo = 
{   
    // It doesn't matter, this is not used in our case
    .deviceInstance     = 0,
    .functionParam      = NULL,
    .idleFunction       = NULL
};
static int16_t accCountsPerG = 512;                 // 512 counts per g as the accelerometer is in the +-4g range (12-bit)
static int16_t gyroCountsPerDegPerSec = 16;         // 16 counts per degree/s as the gyro is in the +-2000 degree/s range (16-bit)
static int16_t magCountsPeruT = 3;                  // 3 counts per uT using the +-1300 uT range from the XY axis (13-bit)
static const float mag_z_scale_factor = 4;          // 2^14 / 2^12. Scaling to make the 2500 uT axis behave as +-1300 uT range

// Mutex
static StaticSemaphore_t sample_mutex_buffer;
static SemaphoreHandle_t sample_mutex;

// Task
static StackType_t stack_fusion[SENSOR_MANAGER_FUSION_STACK_SIZE];
static StaticTask_t task_fusion;
static TaskHandle_t task_handle_fusion;

static StackType_t stack_sensors[SENSOR_MANAGER_SENSORS_STACK_SIZE];
static StaticTask_t task_sensors;
static TaskHandle_t task_handle_sensors;

static void fusion_task(void* arg) 
{
    while(true)
    {
        imu_manager_sample_all();

        sfg.readSensors(&sfg, 1);           
        sfg.conditionSensorReadings(&sfg);  
        sfg.runFusion(&sfg);
        sfg.loopcounter++;

        ESP_LOGV(TAG, "Roll: %.2f, %.2f, %.2f", sfg.SV_9DOF_GBY_KALMAN.fPhiPl, sfg.SV_9DOF_GBY_KALMAN.fThePl, sfg.SV_9DOF_GBY_KALMAN.fPsiPl);

        // Update the data
        if(xSemaphoreTake(sample_mutex, 20 / portTICK_PERIOD_MS))
        {
            sensors_data.gyro = imu_manager_get_gyro();
            sensors_data.acc = imu_manager_get_acceleration();
            sensors_data.mag = imu_manager_get_magnetometer();
            sensors_data.orientation.x = sfg.SV_9DOF_GBY_KALMAN.fPhiPl;
            sensors_data.orientation.y = sfg.SV_9DOF_GBY_KALMAN.fThePl;
            sensors_data.orientation.z = sfg.SV_9DOF_GBY_KALMAN.fPsiPl;
            xSemaphoreGive(sample_mutex);
        }

        // Sample at FUSION_HZ rate
        #if FUSION_HZ > configTICK_RATE_HZ
            #error FUSION_HZ cannot be higher than the RTOS tick rate
        #endif
        vTaskDelay(((1.0F/(float)FUSION_HZ)*1000) / portTICK_PERIOD_MS);
    }
}

static void sensors_task(void* arg)
{
    struct minmea_sentence_gga gps_data;
    unsigned int current_sample_index = 0;

    while(true)
    {
        // Update temperature, pressure, humidity and location every 200 ms
        vTaskDelay(200 / portTICK_PERIOD_MS);

        pressure_manager_do_sample();
        humidity_manager_sample();

        // Update the data
        if(xSemaphoreTake(sample_mutex, 100 / portTICK_PERIOD_MS))
        {
            sensors_data.pressure = pressure_manager_get_pressure();
            sensors_data.temperature = pressure_manager_get_temperature();
            sensors_data.humidity = (uint8_t)humidity_manager_get_humidity();

            if(gps_manager_get_gga(&gps_data))
            {
                sensors_data.latitude = gps_data.latitude;
                sensors_data.longitude = gps_data.longitude;
                sensors_data.altitude = minmea_tofloat(&gps_data.altitude);
                sensors_data.gps_fix = (gps_data.fix_quality == 1 || gps_data.fix_quality == 6) ? true : false;

                // Altitude doesn't have a value yet? 
                if(!got_first_altitude && sensors_data.gps_fix)
                {
                    last_altitude = sensors_data.altitude;
                    altitude_change = 0;
                }
                else if(sensors_data.gps_fix)
                {
                    // Are we lower than the last sample?
                    if(sensors_data.altitude < last_altitude)
                    {
                        altitude_change += sensors_data.altitude - last_altitude;
                    }
                    last_altitude = sensors_data.altitude;

                    // Are we falling?
                    if(fabs(altitude_change) > SENSOR_MANAGER_FALLING_THRESHOLD)
                    {
                        // Open the parachute!
                        servo_manager_open_balloon();
                        servo_manager_open_parachute();
                        ESP_LOGI(TAG, "Fall detection, opening parachute");
                    }
                }
                // TODO: if we don't have a GPS fix we can estimate the height with the pressure sensor
            }

            // Save the current time in us
            sensors_data.timestamp = esp_timer_get_time();
            sensors_data.valid = true;

            // Store the sample
            if(current_sample_index >= SENSOR_MANAGER_MAX_SAMPLES_TO_STORE)
            {
                current_sample_index = 0;
            }
            sensors_samples[current_sample_index++] = sensors_data;

            xSemaphoreGive(sample_mutex);
        }
        else
        {
            ESP_LOGW(TAG, "sensors_task() couldn't get mutex");
        }
    }
}
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

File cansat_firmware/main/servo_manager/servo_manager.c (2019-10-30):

#include "servo_manager.h"
#include "config/cansat.h"
#include "esp_log.h"
#include "driver/ledc.h"
#include "driver/gpio.h"
#include "math.h"

static const uint32_t duty_resolution = 16;
static const uint32_t duty_max = 65536;         // 2^duty_resolution
static const char* TAG = "servo";

// Mutex
static StaticSemaphore_t mutex_buffer;
static SemaphoreHandle_t mutex;

// Status
static bool balloon_opened = false, parachute_opened = false;

static inline void set_servo_duty(ledc_channel_t channel, float duty)
{
    ledc_set_duty(LEDC_HIGH_SPEED_MODE, channel, (uint32_t)((duty*(float)duty_max)/100.0));
    ledc_update_duty(LEDC_HIGH_SPEED_MODE, channel);
}

esp_err_t servo_manager_init(void)
{
    ESP_LOGI(TAG, "Initializing");

    esp_err_t err;

    // Set Timer 0 to generate 50 Hz PWM
    ledc_timer_config_t timer_conf;
	timer_conf.duty_resolution = duty_resolution;
	timer_conf.freq_hz = 50;
	timer_conf.speed_mode = LEDC_HIGH_SPEED_MODE;
	timer_conf.timer_num  = LEDC_TIMER_0;
	if((err = ledc_timer_config(&timer_conf)) != ESP_OK)
    {
        ESP_LOGE(TAG, "Error setting PWM timer");
        return err;
    }

    // Setup the channel for each of the two servos
    ledc_channel_config_t ledc_conf;
	ledc_conf.channel = SERVO_MANAGER_PARACHUTE_CHANNEL;
	ledc_conf.duty = 0;
	ledc_conf.gpio_num = SERVO_PARACHUTE_PIN;
	ledc_conf.intr_type = LEDC_INTR_DISABLE;
	ledc_conf.speed_mode = LEDC_HIGH_SPEED_MODE;
	ledc_conf.timer_sel = LEDC_TIMER_0;
    ledc_conf.hpoint = 0;
	if((err = ledc_channel_config(&ledc_conf)) != ESP_OK)
    {
        ESP_LOGE(TAG, "Error setting channel SERVO_MANAGER_PARACHUTE_CHANNEL");
        return err;
    }

	ledc_conf.channel = SERVO_MANAGER_BALLOON_CHANNEL;
	ledc_conf.duty = 0;
	ledc_conf.gpio_num = SERVO_GLOBO_PIN;
	ledc_conf.intr_type = LEDC_INTR_DISABLE;
	ledc_conf.speed_mode = LEDC_HIGH_SPEED_MODE;
	ledc_conf.timer_sel = LEDC_TIMER_0;
    ledc_conf.hpoint = 0;
    if((err = ledc_channel_config(&ledc_conf)) != ESP_OK)
    {
        ESP_LOGE(TAG, "Error setting channel SERVO_MANAGER_BALLOON_CHANNEL");
        return err;
    }

    // Create mutex for this resource
    mutex = xSemaphoreCreateMutexStatic(&mutex_buffer);

    // Close at startup
    servo_manager_close_parachute();
    servo_manager_close_balloon();

    ESP_LOGI(TAG, "Ready!");

    return ESP_OK;
}

bool servo_manager_open_parachute(void)
{
    if(xSemaphoreTake(mutex, 200 / portTICK_PERIOD_MS))
    {
        set_servo_duty(SERVO_MANAGER_PARACHUTE_CHANNEL, SERVO_MANAGER_PARACHUTE_OPEN_SERVO_DUTY);
        parachute_opened = true;
        xSemaphoreGive(mutex);
        return true;
    }
    return false;
}

bool servo_manager_close_parachute(void)
{
    if(xSemaphoreTake(mutex, 200 / portTICK_PERIOD_MS))
    {
        set_servo_duty(SERVO_MANAGER_PARACHUTE_CHANNEL, SERVO_MANAGER_PARACHUTE_CLOSE_SERVO_DUTY);
        parachute_opened = false;
        xSemaphoreGive(mutex);
        return true;
    }
    return false;
}

bool servo_manager_open_balloon(void)
{
    if(xSemaphoreTake(mutex, 200 / portTICK_PERIOD_MS))
    {
        set_servo_duty(SERVO_MANAGER_BALLOON_CHANNEL, SERVO_MANAGER_BALLOON_OPEN_SERVO_DUTY);
        balloon_opened = true;
        xSemaphoreGive(mutex);
        return true;
    }
    return false;
}

bool servo_manager_close_balloon(void)
{
    if(xSemaphoreTake(mutex, 200 / portTICK_PERIOD_MS))
    {
        set_servo_duty(SERVO_MANAGER_BALLOON_CHANNEL, SERVO_MANAGER_BALLOON_CLOSE_SERVO_DUTY);
        balloon_opened = false;
        xSemaphoreGive(mutex);
        return true;
    }
    return false;
}

bool servo_manager_is_parachute_open(void)
{
    return parachute_opened;
}

bool servo_manager_is_ballon_open(void)
{
    return balloon_opened;
}

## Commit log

2018-09-12 Agregada la estructura de archivos relacionados al Hardware
    Hardware/EstacionTerrena y Hardware/satelite
    [EstacionTerrena.kicad_pcb, EstacionTerrena.sch, Satelite.kicad_pcb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]
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2018-09-12 Agregado logo en el esquematico de la estacion
    [CC1101.sch, EstacionTerrena.sch, USBaSPI.sch]
2018-09-13 Esquema de estación terrena casi terminado. falta revision.
    [CC1101.sch, EstacionTerrena.sch, USBaSPI.sch]
2018-09-13 Correciones en esquema de estacion terrena y agrege descripciones a libs
    [USBaSPI.sch]
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2018-09-17 Estructura preliminar del mecanismo de liberación del paracaídas
    [SG90 - Micro Servo 9g - Tower Pro.1.SLDPRT, SG90 - Micro Servo 9g - Tower Pro.2.SLDPRT, SG90 - Micro Servo 9g - Tower Pro.3.SLDPRT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]
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2018-09-17 Más cambios al sistema de sujeción del paracaídas
    [actuadoresSat.SLDASM, cuerpoSat.SLDPRT, pisoParacaida.SLDPRT]
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2018-09-17 Agrege limite de movimientos en los brazos de servos
    [SG90 - Micro Servo 9g - Tower Pro.SLDASM, actuadoresSat.SLDASM]
2018-09-17 Cambios en los agujeros para el montaje de los actuadores y los PCB
    [actuadoresSat.SLDASM, asmCanSat.SLDASM, cuerpoSat.SLDPRT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]
2018-09-18 Brazo de servos modificado para evitar colisiones en sus movimientos
    [actuadoresSat.SLDASM, asmCanSat.SLDASM, brazoServo.SLDPRT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]
2018-09-18 Adición de refuerzos a la estructura del satélite y ventilas
    [actuadoresSat.SLDASM, asmCanSat.SLDASM, cuerpoSat.SLDPRT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]
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2018-10-02 Mejoras en la estructura del CanSat para facilitar el montaje
    [asmCanSat.SLDASM, pisoParacaida.SLDPRT, tapaSuperiorSat.SLDPRT]
2018-10-02 Aumentado el diametro de la estructura del CanSat a 66 mm
    [actuadoresSat.SLDASM, asmCanSat.SLDASM, baseSat.SLDPRT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]
2018-10-02 Pequeños cambias de alineación al modelo del satélite
    [asmCanSat.SLDASM, baseSat.SLDPRT, cuerpoSat.SLDPRT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]
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2018-10-02 Esquema inicial para fuel gauge en PCB_A y inicio de esquemas para PCB_B
    [CC1101.sch, Cargador de batería.sch, Fuel Gauge.sch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]
2018-10-03 Algunos arreglos:
    - Tornillos de agarre de los actuadores del satélite
    - Los topes para el cierre de los servos son piezas apartes ahora para facilitar la impresión
    [actuadoresSat.SLDASM, asmCanSat.SLDASM, pisoParacaida.SLDPRT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]
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2018-10-11 Agregado logo y cambio de posición de LEDs a PCB de estación terrena
    [EstacionTerrena.sch, _saved_EstacionTerrena.sch]
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2018-10-12 Cambio de MCU supervisor de F4 a F3 y agregado de protecciones
    [PCB_B.sch, PCB_C.sch, _saved_EstacionTerrena.sch]
2018-10-12 Agregado jumper para pin BOOT0 y capacitores para los pines de comparadores
    [PCB_B.sch]
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2018-10-15 PCB_D agregado LED para blink + boton reset. Creado netlist
    [PCB_D.sch]
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2018-10-15 PCB_C: Cambiado conector externo y pequeño arreglo en texto descriptivo
    [PCB_C.sch]
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2018-10-16 Conector de expansion fix
2018-10-16 PCB_E fix netlist
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2018-10-16 PCB_D arreglado y serigrafias acorde a nueva disposicion de pines del conector de expansion
    [Con_Expansion_IO.dxf, Con_Expansion_IO_Mirror.dxf, Con_Expansion_IO_Mirror_R12.dxf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]
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2018-10-17 Trazas más gruesas para VBat y corrección de error DRC en PCB_A
    [PCB_A.kicad_pcb]
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2018-10-17 Switch analógico para cambiar entre los niveles de tensión de los buffers en PCB_C
    [PCB_C.sch]
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2018-10-18 PCB inicial para PCB_B y footprint de conector entre los PCB B-C (WIP)
    [PCB_B.sch]
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2018-10-25 La parte del conector B-C que va en el PCB_B fue movido a bottom mientras que la parte que va en el PCB_C permanece en top
    [PCB_B.kicad_pcb, PCB_B.sch, PCB_C.kicad_pcb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]
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2018-10-25 Revert "PCB B WIP"
    This reverts commit 7e9720afefe395d959b0157ab5be25ebb8bd8a98.
    [PCB_B.kicad_pcb, PCB_B.sch, Power 3V3.sch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]
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2018-11-06 IO3 y IO4 del PCB C al conector de expansión son ahora también UART3 del MCU supervisor
    [PCB_C.kicad_pcb, PCB_C.sch]
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2018-11-06 Numeros de parte para PCB_A. Se movió también el switch de encendido más afuera para fácil acceso.
    [CC1101.sch, GPS.sch, PCB_A.kicad_pcb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]
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2018-11-07 Numeros de parte para estación terrena. Capacitores de 15pF para cristal de CC1101 (en lugar de 18pF).
    [CC1101.sch, USBaSPI.sch]
2018-11-07 Agregado boton de reset para Arduino en PCB_D
    [PCB_D.sch, USBaSPI.sch]
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2018-11-08 Separadores de 12mm entre A y B para dar lugar a la bateria
    [Hex Spacer MF M3 L12mm.SLDPRT, PCB_B.sch, asmCanSat.SLDASM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]
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2018-11-08 Modificado conector A-B para poder alojar la batería entre A y B
    [PCB_A.SLDPRT, PCB_A.kicad_pcb, PCB_A.step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]
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2018-11-08 Eliminado switch de 5V y 3.3V y corrección en pines de SPI al CC1101 en PCB_C
    [PCB_C.kicad_pcb, PCB_C.sch]
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2018-11-08 Agregados logos en PCB_D y headers con tx y rx para debug
    [PCB_D.sch]
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2018-11-13 Arreglado bug de pantalla blanca en build
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2018-11-15 Correccion de errores de compilacion en linux
    [cansat.h, main.c]
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2018-12-26 Cambios iniciales en el esquema de PCB_C para utilizar el EPS32 en lugar del STM32F303RE
    [PCB_C.sch]
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2018-12-28 Cambios en PCB_C para el nuevo conextor de expansión que lleva VBus ahora
    [PCB_C.sch]
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2018-12-28 Agregado a estación terrena el capacitor de bloqueo para el balun 885012005046
    [CC1101.sch]
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2018-12-28 Corrección de errores de conexión en pines del ESP32
    [PCB_C.sch]
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2018-12-28 Uso de 3.3V internos para todos los sensores en PCB_C y agregado de divisor resistivo para la señal de 5V proveniente del BQ24392.
    [IMU.sch, PCB_C.sch, Sensor presión.sch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]
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2018-12-29 Arreglos serigrafía PCB_E
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2018-12-31 Eliminadas resistencias del bus I2C redundantes en PCB_B (ya están en PCB_C)
    [Fuel Gauge.sch]
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2018-12-31 Nuevo circuito en PCB_D para permitir recepción desde el UART del ESP32 y del USB
    [PCB_D.sch]
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2019-01-02 Agregado pull-up para CBUS3 del FT231XS faltante y corregido D+ y D- invertidos en PCB_D
    [PCB_D.sch]
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2019-01-09 Agregado polyfuse para VBUS y designadores a los test points en PCB_B
    [PCB_B.sch]
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2019-01-10 Pequeño arreglo para prevenir redirección al soltar un archivo en la app
2019-01-11 Cambios en el valor del divisor resistivo de la fuente de 3.3V y en el filtro anti-aliasing de tensión de la fuente de 5V
    [Power 3V3.sch, Power 5V.sch]
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2019-01-17 Reducido el tamaño del cuerpo del satelite para no superar los 115mm de altura
    [cuerpoSat.SLDPRT, postizoCuerpoSat.SLDPRT]
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2019-01-21 Primer commit eliminando RIOT OS y código inicial para FreeRTOS en el ESP32
    [uncrustify-riot.cfg]
2019-01-21 Arreglo en sistema de notificaciones
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2019-01-22 Más managers, mejor manejo de errores, más codigo, un poco de todo XD
    [aux_ps.c, cansat.h, gps_manager.c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]
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2019-01-25 Mejoras, corrección de bugs, agregado de logging y sensor de presión 100% funcional
    [gps_manager.c, i2c_manager.c, main.c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]
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2019-01-27 Agregado más manejo de errores
    [imu_manager.c, main.c, sensor_manager.c]
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2019-01-29 Corrección de error en i2c_manager no enviando la dirección del registro a modificar
    [i2c_manager.c, imu_manager.c]
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2019-01-29 Sensor fusion de 9 DOF (aun hay problemas con el drift)
    [imu_manager.c, sensor_manager.c, sensor_manager.h]
2019-01-29 Corrección de constantes para la libreria de fusion sensor y eliminación de la mayor parte del drift (aun existe algo de drift en pitch)
    [imu_manager.c, sensor_manager.c]
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2019-01-31 Corrección de errores por NULL pointer esporádicos en sensor_manager
    [sensor_manager.c]
2019-01-31 Corección de error de NULL pointer en gps_manager
    [gps_manager.c]
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2019-01-31 Múltiples bugs en led_manager corregidos
    [led_manager.c, main.c]
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2019-01-31 Fix para que se ocupe el 100% de la pantalla al iniciar app
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2019-02-04 Mejor logging de errores en sensor de presión y humedad
    [humidity_manager.c, pressure_manager.c]
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2019-02-04 Corrección de bug en driver de bq27441 no entrando al modo configuración
2019-02-05 Reducción del clock del bus I2C interno a 20 kHz para correcto funcionamiento con fuel-gauge
    [i2c_manager.c]
2019-02-05 Múltiples bugs corregidos en driver de bq27441
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2019-02-05 Agregada lógica de carga de misiones y arreglos
2019-02-05 Corrección de bugs y comprobaciones adicionales en driver de CC1101
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2019-02-06 Nuevos arreglos en lógica de creación y guardado de misiones
2019-02-06 Varios bugs corregidos en driver de CC1101. Transmición funcionando correctamente ahora.
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2019-02-08 Pequeño bug en carga de misiones arreglado
2019-02-08 Corrección de errores de compilación
    [com_manager.c]
2019-02-09 Corrección de error donde rx_task nunca podía tomar el mutex para el control del transceiver
    [com_manager.c]
2019-02-09 Corrección de múltiples errores en PIC16 y recepción de datos en el ESP32
    [cansat.h, i2c_manager.c, i2c_slave_manager.c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]
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2019-02-10 Agregado envío de errores
    [com_manager.c, power_monitor.c, power_monitor.h]
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2019-02-11 Arreglo de funciones en driver CC1101 de javascript
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2019-02-12 Corrección de varios errores en el driver de CC1101 de javascript
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2019-02-12 Corrección de errores en recepción y decodificación de paquetes
    [com_manager.c]
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2019-02-13 Cambiado CLI provisto por Microchip por uno propio debido a bugs que presentaba
2019-02-13 Correccion de algunos bugs e integración del nuevo CLI
    [com_manager.c]
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2019-02-14 Corregido error donde corrientes de 5V y batería y tensión de 5V eran reportadas como 0
    [power_monitor.c]
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2019-02-17 Cambios en la lógica de envío de errores con el comando 0x00
    [com_manager.c]
2019-02-17 Agregada logica para ocultar sensores y pequeños arreglos
    [caja et.SLDPRT]
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2019-02-18 Carga de muestras, errores y actuadores + arreglos en modelo et
    [caja et.SLDPRT]
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2019-02-18 Corrección de error en com_manager cuando el mutex no podía ser tomado se accedía al CC1101 de todas formas. También se cambió el método de envío automático intercalando entre sensores y datos de cor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
    [com_manager.c]
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2019-02-19 Arreglo de unidades y gráficos
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2019-02-20 Cambios en la manera de enviar errores a la estación terrena
    [com_manager.c]
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2019-02-20 Agregado indicador de fix de GPS al sensor de posición
    [com_manager.c]
2019-02-20 Arreglos en la UI
2019-02-20 Carga de mision arreglada
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2019-02-20 Arreglado bug de nombre de cansat en mision
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2019-02-20 Worker modificado la app pide siempre a cansat excepto los errores
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2019-02-22 Re enumeración de codigos de errores
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2019-02-23 Correccion en el modo de SPI y errores en generacion del checksum en el conversor USB-SPI
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2019-02-25 Corrección de error en cómputo de checksum de paquetes
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2019-02-25 Corrección paquete CANSAT_ENABLE_DISABLE_PS no respondía de manera correcta
    [com_manager.c]
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2019-02-25 Arreglos en la activación de fuentes
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2019-02-25 Pequeños arreglos en UI y en creación de proyecto
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
